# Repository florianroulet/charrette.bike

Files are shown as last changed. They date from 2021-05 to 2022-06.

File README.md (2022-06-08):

# CHARRETTE: CHARRETTE Hardi Auto-freinante Remorquable Réservable Esthétique Tractable Tenace Électrique

origine : https://framagit.org/Veloma/Charrette

## Description
Charrette est une remorque à vélo à trois roues avec système  de  freinage  inertiel et un système d’assistance électrique autonome.
 * Pensée  pour  l’autoconstruction  et  une  diffusion large, la remorque s’attelle sur toutes les tiges de selle de vélo  ou se tire à la main.
 * Le  mécanisme  du  frein  à  inertie  automatique  protège remorque et cycliste en permettant d’augmenter la charge utile jusqu’à 300 kg.
 * Le format de chargement est prévue pour la vélologistique sur palette ou boites transport Euro.
 * Une assistance électrique est conçue pour que la charrette accompagne indépendamment le vélo en modulant sa  propre puissance.
 * D’autres éléments déployables, solaires ou fonctionnels  assurent une grande variété d’usages (restauration, culturel, social....).
 * La remorque en source libre est conçue en tubes carrés simples à provisionner et facilement soudable.

### Historique selon la Charrette
Moi, la charrette, remorque à vélo dont la conception a été commencée et est maintenue à ce jour par Véloma, je suis le fruit d'un long cheminement, d'itérations successives, d'expérimentations pour obtenir un engin roulant tractable à vélo stable et efficace.
Ce chemin a croisé celui d'amis, de personnes désireuses de donner un avis ou dans le besoin de livrer des plantes en moins d'une heure de l'autre côté d'une ville trop chargée par des véhicules vides. Sur la route, j'ai rencontré l'ADEME, au travers d'un Appel à Manifestation d'Intérêt de l'agence francilienne lancé en mai 2020. Cet AMI avait pour thème les basses-technologies, ou low-tech.

Voici quels sont les objectifs énoncés par [cet appel à projet](/pdf/AMI.pdf)

>Ouvert, ascendant et promouvant des approches **résolument systémiques de l'innovation**, le présent AMI poursuit plusieurs objectifs **dans une perspective d’autonomie, d’autosuffisance, d’adaptabilité, de transformabilité et de résilience territoriales** :
>
>* Questionner l’organisation socioéconomique et territoriale des activités humaines à l’aune de l’échelle bien proportionnée pour la mise en œuvre d’une démarche « low- tech » : modèles organisationnels, modèles d’affaires, synergies et solidarités interterritoriales, etc. ;
* Interroger les besoins en ressources au regard des limites physiques (finitude des ressources, etc.), technico-économiques (phénomène de saturation des capacités des systèmes techniques, taux de retour énergétique décroissants des ressources énergétiques, endettements, rendements théoriques maximaux, rendements décroissants des systèmes complexes, etc.) et humaines (résistances au changement de comportement) : sobriété, écologie de la demande, etc. ;
* Étudier, dans toutes leurs dimensions (technologique, fiscale, législative, réglementaire, normative, etc.), les conditions d’émergence ainsi que les freins et les leviers au (re)déploiement de systèmes sociotechniques et économiques plus intensifs en emplois et plus sobres en consommation de ressources. Il s’agira ici de s’interroger sur la quantité et la qualité du travail humain et de caractériser ce que seraient des métiers et des emplois « low-tech » ainsi que les trajectoires de reconversion professionnelle associées dans les prochaines décennies à l’aune de la notion d’« esclave énergétique » et dans un contexte d’accès aux ressources (énergétiques notamment) de plus en plus limité. En particulier, seront-ils plus ou moins salariés, plus ou moins rémunérés, plus ou moins partagés, plus ou moins réflexifs et scientifiquement éclairés, plus ou moins manuels, plus ou moins physiques ?
* Contribuer à remettre de la lucidité et de redonner du sens à l’innovation et à réinventer des métiers et emplois inspirants compatibles avec la réalité physique d’un monde fini par la transformation des récits collectifs aujourd’hui dominés par le paradigme de l’inflation technologique et de l’accumulation matérielle.

Alors que j'étais en prototypage dans l'atelier de Véloma, alors que le monde entier et la France en particulier étaient enfermés entre quatre murs, mes trois pneus se gonflaient, on m'accrochait derrière un vélo et je m'élançais dans les rues séquano-dyonisiennes pour livrer denrées et semis.
Pendant ce temps, Véloma a envoyé un dossier à l'ADEME et est devenue, comme 9 autres structures, lauréate de cet appel à manifestation d'intérêt.

J'ai ainsi été propulsée sous les feux d'une petite communauté de bricoleurs, de créateurs, de rêveurs qui oeuvrent pour créer un autre monde, un monde où l'on pourrait aller faire ses courses avec son vélo, un monde où l'on pourrait m'emprunter ou me louer dans une maison de quartier, un monde où l'on pourrait télécharger mes plans sur internet pour les donner au soudeur du coin et qu'une soeur naisse ailleurs, un monde où l'on pourrait m'augmenter, me transfigurer, m'adapter à des usages non prévus lors de ma conception.

Ce monde décrit à l'instant, c'est celui vers lequel me porte Véloma avec l'aide de l'ADEME, du réseau mis à disposition et des copains dont tu peux faire partie. Je suis sur cette route depuis novembre 2020 et jusqu'à octobre 2022.

## Libre, auto-constructible et réparable
Les concepteurs initiaux de la remorque croient en un monde inspiré du logiciel libre, un monde qui n'a pas peur de partager ses connaissances pour les voir être appropriées par d'autres, améliorées, modifiées ou détournées.
Ainsi l'intégralité des plans de la charrette seront mis à disposition sur ce site sous licence CERN-OHL-W v2. Le code sera partagé sous licence CC-BY-SA.

## La remorque
La remorque est un engin roulant à trois roues qui s'attele sur la tige de selle d'un vélo.
Elle peut aussi être tractée par un humain voire un animal de traie.
La structure et les roues ont été dimensionnées pour supporter 300kg.
La surface utile de chargement est de 1705x650mm, les ridelles font 330mm de haut, la garde au sol est de 360mm.

### Structure
Les tubes de la structure sont soudés ensemble pour assurer rigidité et longue vie au châssis.
Des plans de découpe laser des tubes existent mais la découpe à la main de chaque tube est possible.

Nous travaillons avec de l'acier inox 304 et 316 mais il est possible d'utiliser n'importe quel acier de qualité, un passage à la peinture sera à considérer.

Pour la soudure, nous avons des postes TIG et MIG dans notre atelier mais lors des formations, la soudure à l'arc avec baguette inox est utilisée.

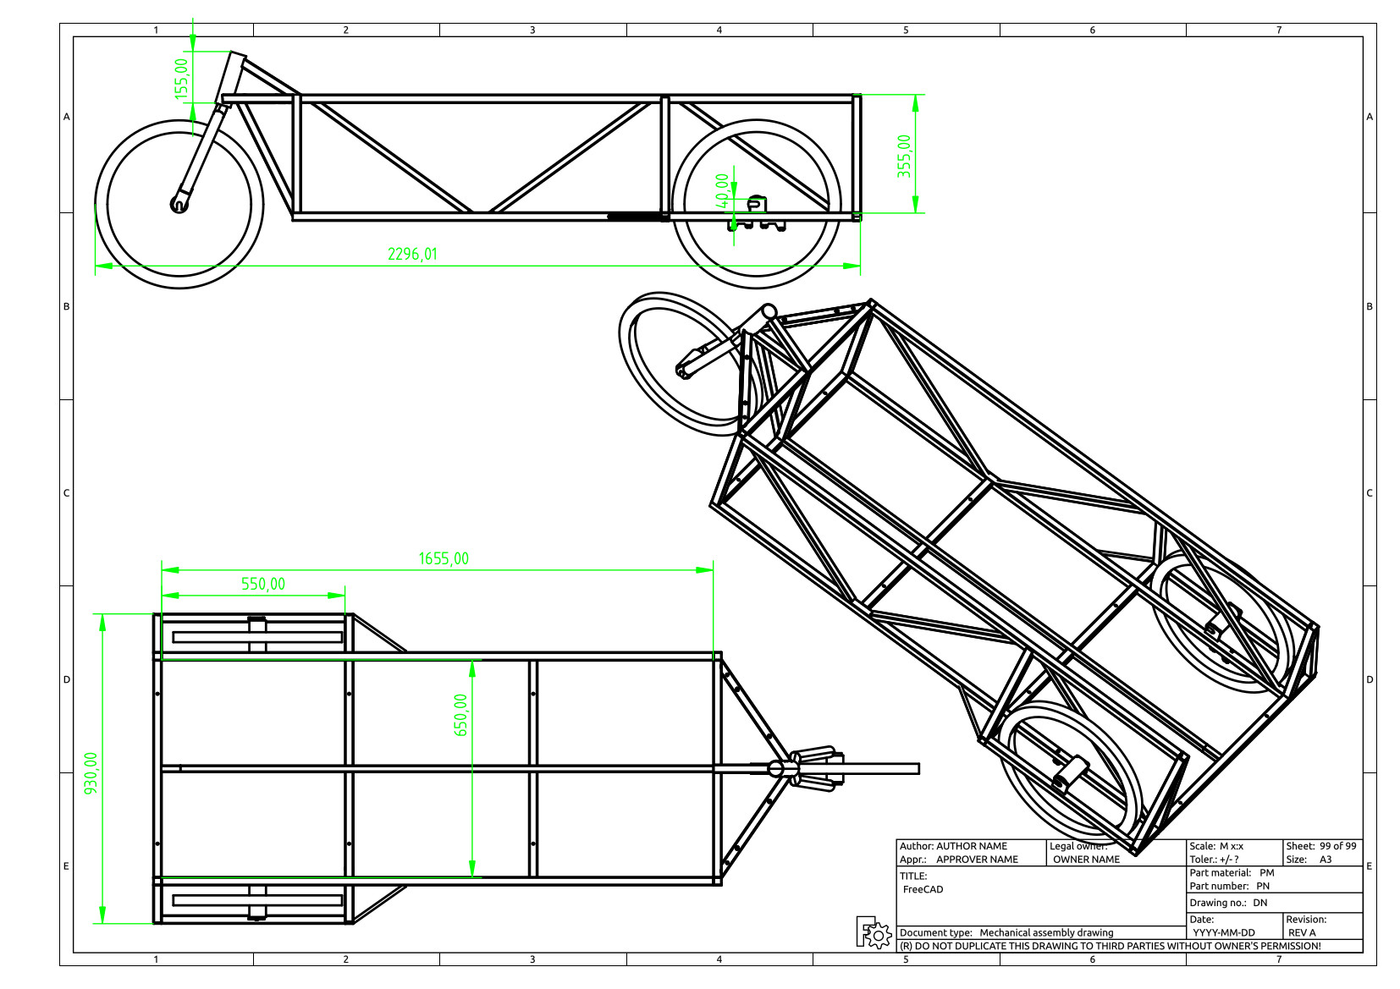
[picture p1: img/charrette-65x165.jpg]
Châssis de la remorque


Une réflexion est menée pour la fabrication de fourche 20":

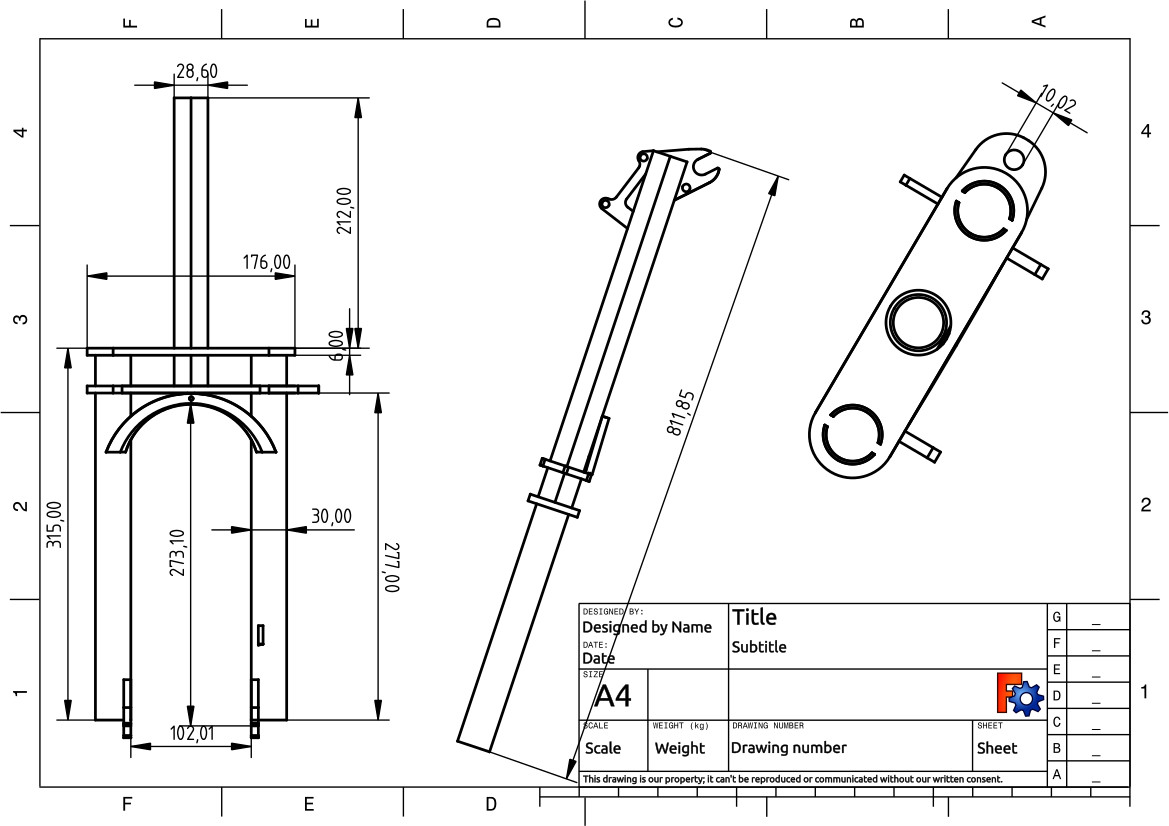
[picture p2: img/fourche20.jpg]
Fourche 20"


### Equipement vélo
La charrette est un équipement de cycles et à ce titre est équipée comme un vélo:
* Jantes kargo;
* Rayons inox renforcés;
* Moyeux renforcés;
* Garde-boue en aluminium;
* Axes de roues diamètre 15 en acier plein et faits chez un tourneur;
* Freinage à câble;
* Etrier de frein à disque BB5;
* Jeu de direction interne;
* Potence courte.

Tous ces équipements sont au maximum sourcés en France ou en Europe.
Une attention toute particulière a été portée aux roues que nous assemblons nous-mêmes afin qu'une charge de 300kg soit supportées dynamiquement entre les trois roues et axes.

### Système de freinage inertiel
Un mouvement relatif entre la barre d'attelage et la remorque est autorisé par un roulement linéaire dans le sens de la marche.
Un ressort limite les mouvements et tend à maintenir la remorque dans une position au repos.
En cas de freinage du pilote, la remorque vient s'appuyer sur la barre d'attelage et tire deux câbles qui freinent les roues arrières.
Il s'agit là d'un frein à inertie qui est primordial pour la tenue de route et la sécurité du chargement.

### Frein de stationnement
A l'arrêt, pour sécuriser la Charrette, il est possible de maintenir le frein à inertie actionné avec un crochet. Le frein à inertie devient alors frein de stationnement.

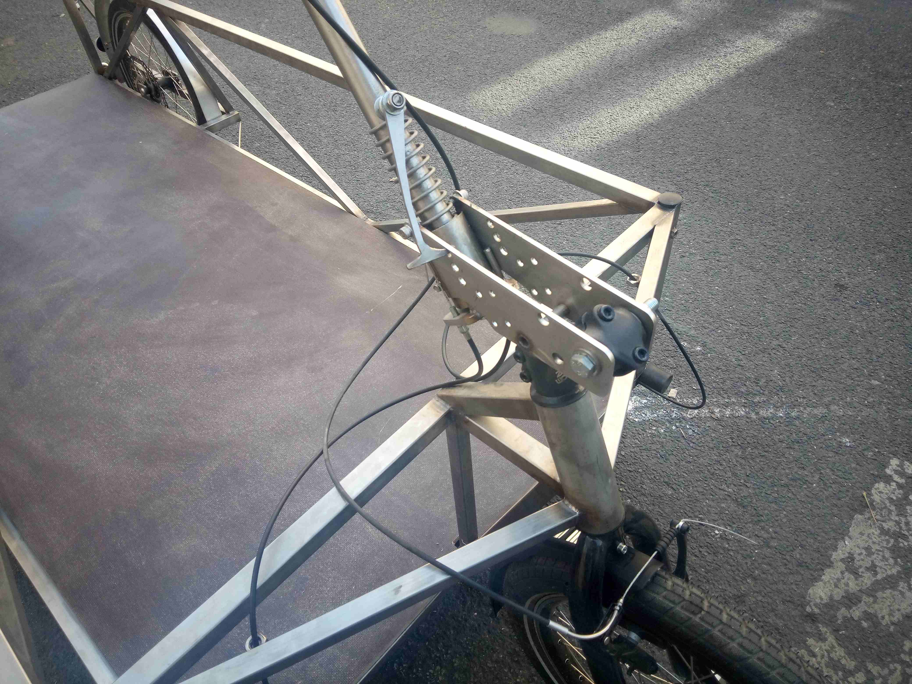
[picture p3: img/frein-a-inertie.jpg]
Frein à inertie et de stationnement


### Tenue de route
Nous n'avons pas encore réussi à retourner la charrette dans un virage.

## Assistance électrique

Là où les vélos sont limités à 250W, les remorques à vélo n'observent pas cette limite tant qu'elles ne sont pas motrices, entendez qu'elles ne poussent pas le vélo.sdfdsf
Le système d'assistance électrique met donc la remorque en équilibre derrière le cycliste et active même le freinage moteur en cas de besoin.
Nous préconisons un moteur de 1200W et une batterie de 48V afin d'avoir assez de puissance pour déplacer jusqu'à 300kg, il faudra tout de même appuyer sur les pédales.

A minima il faudra donc s'équiper:
* d'un moteur moyeu 1000/1500W monté dans une roue 20"
* d'un contrôleur de moteur 48V 25A
* d'une batterie de 48V 20Ah

Deux types d'assistance ont été développés:
 - Une assistance "intelligente" qui détecte le retard de la remorque par rapport au cycliste et assiste en fonction.
 - Une assistance manuelle qui est pilotée par une gachette au guidon du cycliste.

### Assistance "intelligente"

En équipant la barre d'attelage de jauge de contrainte, il est possible de piloter l'assistance électrique avec un arduino.
Ce système est mis sous tension par un simple interrupteur, ensuite sitôt que la remorque détecte qu'elle est en retard par rapport au vélo, elle actionnera son moteur jusqu'à rattraper le cycliste et dans le cas contraire où elle ira plus vite, la remorque ralentira voire activera son frein moteur.
Cette assistance, plus simple à l'utilisation car il n'y a aucune modification à apporter au vélo-tracteur, est aussi plus compliquée à mettre en oeuvre soit-même et dépend de composants électroniques supplémentaires à approviosionner et à assembler.

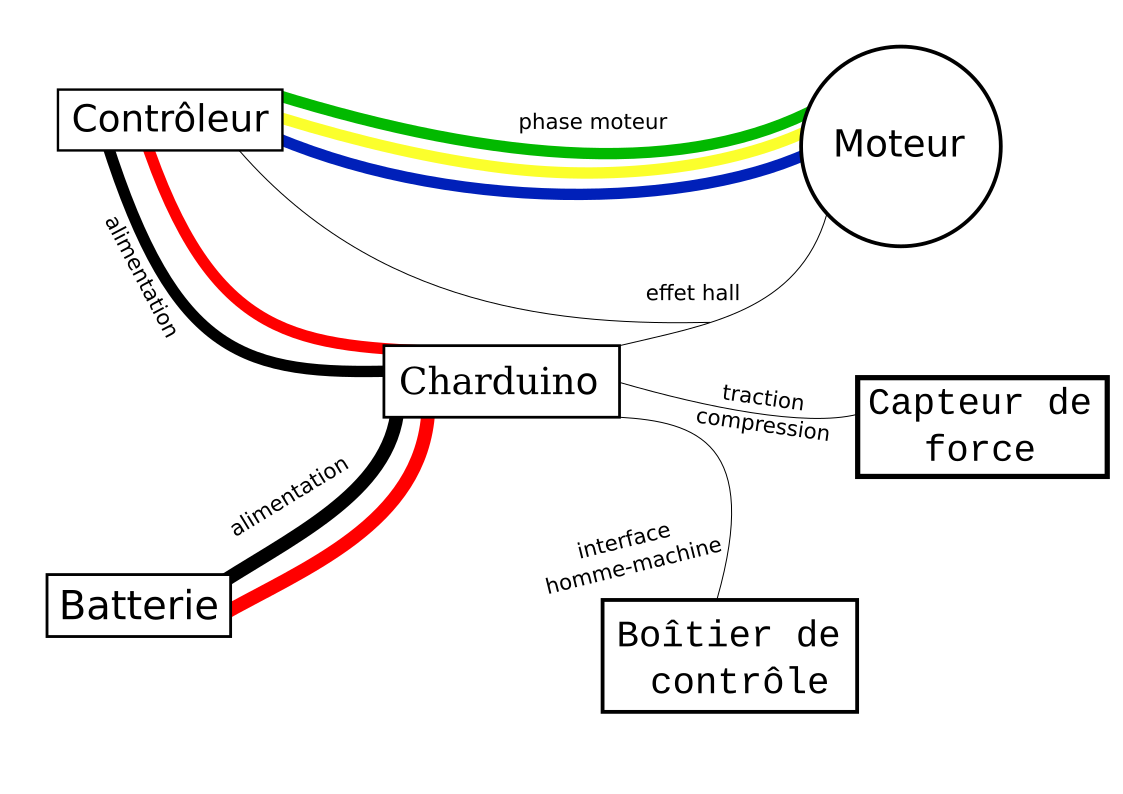
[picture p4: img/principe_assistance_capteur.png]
Schéma de principe


### Assistance manuelle

Les systèmes d'assistance électrique standard peuvent fonctionner avec une gachette d'accélération. L'exemple en est des trottinettes électriques.
Il est possible de piloter la Charrette avec une gachette en tirant un câble jusqu'au guidon.
Pour rester mettre de la remorque, et aussi rester dans le cadre de la loi française, il est impératif que le vélo reste tracteur et ne soit pas propulsé par la Charrette.
En équipant le frein à inertie d'un contacteur, il est possible de couper le signal envoyé au contrôleur. Sitôt que la remorque vient appuyer sur le vélo, le frein à inertie s'enclenche, le contacteur aussi ouvrant le circuit et coupant l'assistance. L'ajout d'un circuit RC entre le contrôleur et le contacteur permet de lisser les accélérations et déccélérations.
Cette solution est plus facile à mettre en oeuvre pour le constructeur mais moins comode pour l'usager qui doit préparer son vélo avant de partir.
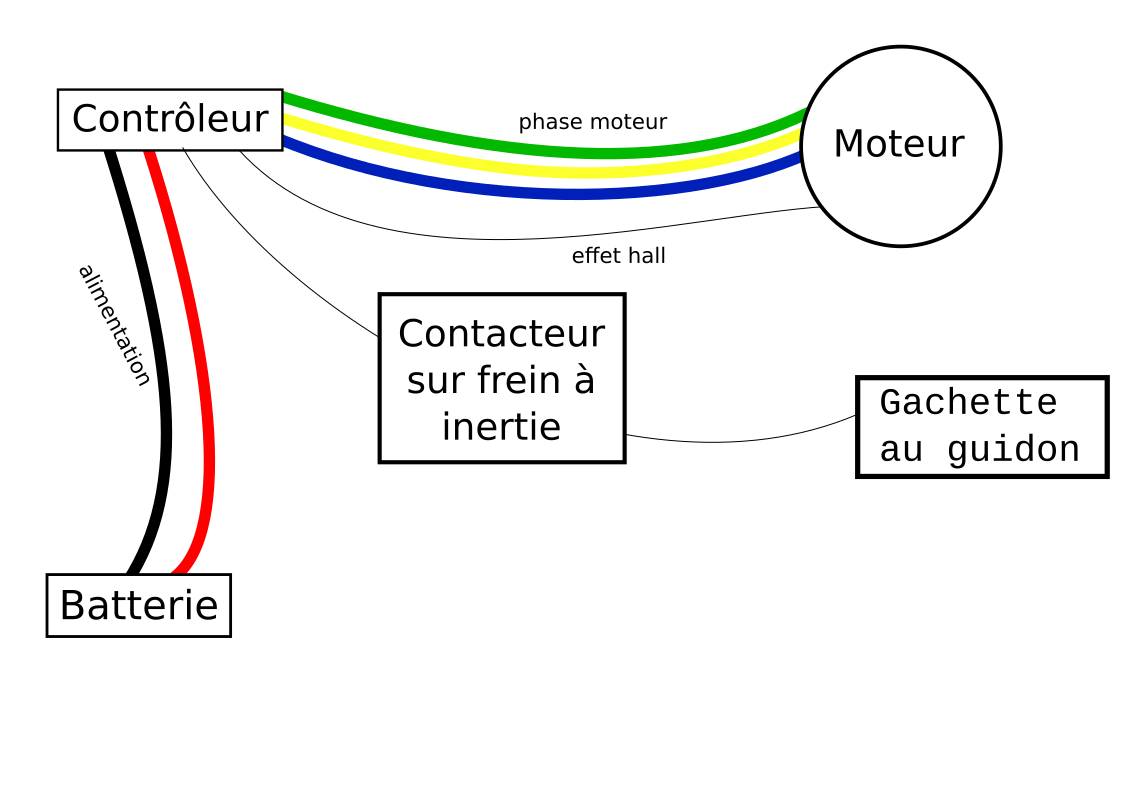
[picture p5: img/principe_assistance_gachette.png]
Schéma de principe


## Système de partage

Un système informatique, pas encore disponible, permettra de mutualiser l'utilisation d'une charrette ou de n'importe quel vélo, pour étendre les imaginaires de toute un quartier. Le code s'appuiera sur celui d'[Open Source Bikeshare](https://github.com/cyklokoalicia/OpenSourceBikeShare).

Ce système de partage a vocation à fonctionner sur un ordinateur type Raspberry Pi et pourra tout aussi bien gérer la mutualisation d'une charrette que de vélos en partage.

## Modulaire

La charrette peut être modifiée facilement et gagner de nouvelles fonctionnalités.

### Charrette-Pikip
Ainsi il est possible d'ajouter des panneaux solaires par exemple et une enceinte [Pikip](https://www.pikip-solarspeakers.com) pour transformer la charrette en remorque Boum-Boum, un engin de célébrations massives.

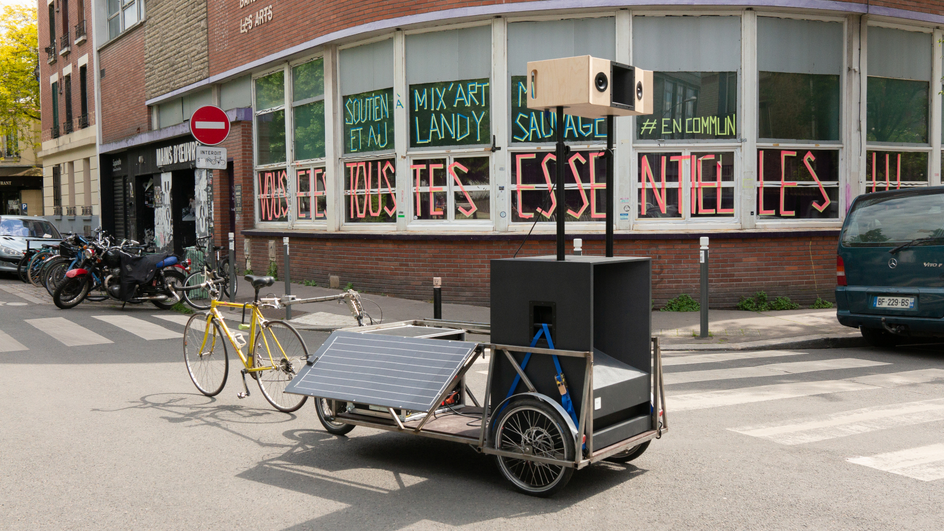
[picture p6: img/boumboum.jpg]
Boumboum


### Panneaux déployables
Les tubes verticaux sont pensés comme chandeliers pour accueillir d'autres tubes et ainsi autoriser le pivotement de panneaux.
Un exemple d'une charrette utilisée par l'association Déenbulles, une ludothèque itinérante.

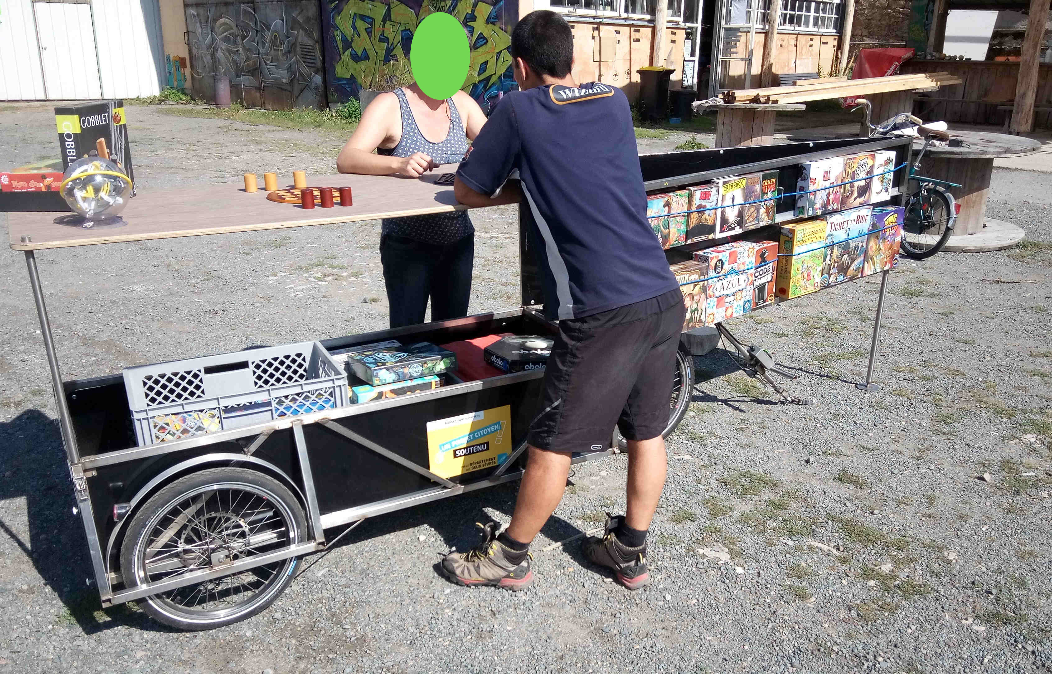
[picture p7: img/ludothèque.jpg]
Ludothèque


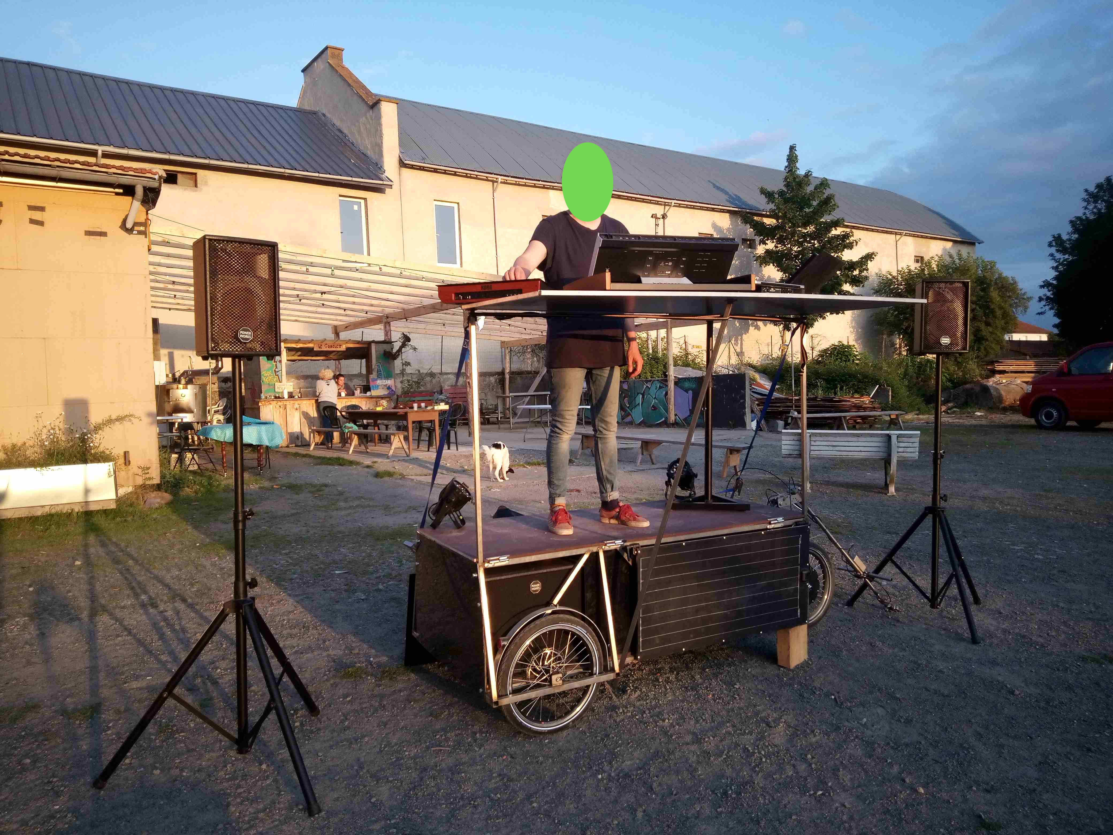
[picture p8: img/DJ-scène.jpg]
DJ Scène


### Examples d'utilisations:

Davantage de photos sur [Charrette.bike](https://charrette.bike)
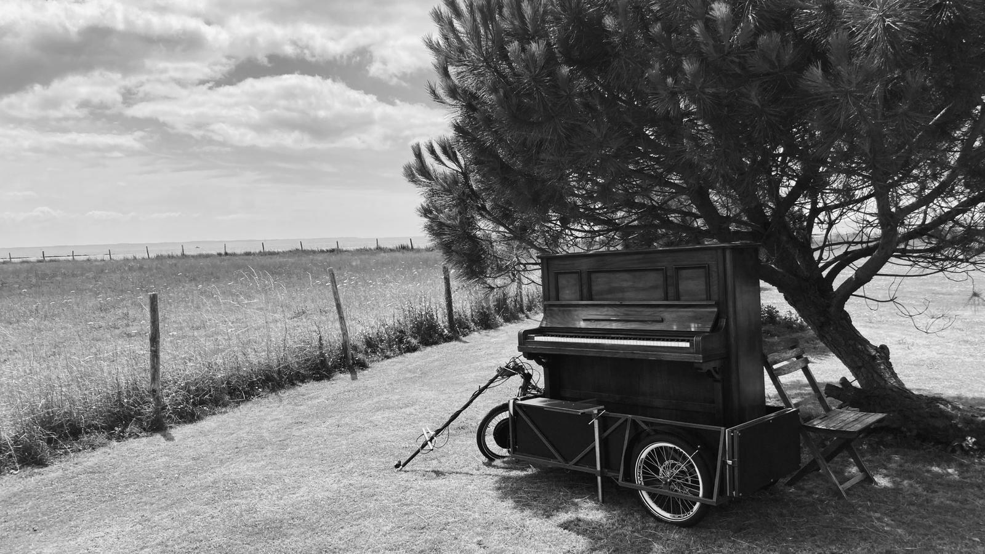
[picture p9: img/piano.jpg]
Piano


## Coût de revient

Le temps passé à chercher et acheter les composants n'est pas pris en compte.

| Partie | Description | Total |
| --- | ---  | --- |
| Structure | Tubes, boulonnnerie, consommable soudure, ...| ???? |
| Equipement vélo | Roues, câbles, gaines, ... | ???? |
| Electronique Charduino| Composants, câbles, connecteurs | ???? |
| Electronique assistance| Moteur, contrôleur, batterie | ???? |
| Total| Matériel | ???? |

## Temps d'assemblage

Le temps passé à chercher, dessiner et/ou acheter les composants n'est pas pris en compte. On considère que les différentes techniques nécessaires sont déjà acquises à la personne qui assemble.

| Partie | Description | Total |
| --- | ---  | --- |
| Structure | Mise en place, sous contrainte, soudure, nettoyage | 2 jour |
| Equipement vélo | Rayonnage des deux roues arrière, installation des composants, réglage des freins | 1,5 jours |
| Electronique Charduino| Soudure des composants, connectiques | 1 jour |
| Electronique assistance| Préparation connectique, branchement | 0,5 jour |
| Total| Temps passé pour une charrette | 5 jours |

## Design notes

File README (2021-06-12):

Arduino pour contrôler la remorque en fonction du capteur de traction

Bibliothèques requises:

#include <EEPROM.h>
#include <Chrono.h>
#include <SoftFilters.h>
#include <PID_v1.h>
#include <Adafruit_NeoPixel.h>
#include <HX711_ADC.h>

2020 11 09
Jusqu'à présent l'arduino était alimenté par le contrôleur via le 5V de la gachette.
Lors des essais il a été constaté qu'il redémarrait quand le moteur tirait trop de jus.
On va passer sur une alimentation directement par la batterie, incorporation d'un step-down pour passer de 36V à 5V et avoir ainsi une alim stabilisé.

Le 5V de la gachette sera tout de même utilisé pour savoir si le contrôleur est allumé ou pas, utilisation d'une résistance pull-down sur une pin.
Possibilité d'utiliser un transistor pour activer le contrôleur quand l'arduino est prêt et que la barre de traction est prête.
Ainsi quand on verra que le contrôleur ne répond pas, on pourra l'éteindre et le rallumer.

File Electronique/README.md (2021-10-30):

# Electronique

Sera évoquée ci-dessous l'électronique de l'assistance électrique utilisant un capteur de force. Il s'agit du Charduino, contraction de Charrette et Arduino.

Pour rappel voici un schéma de principe:

Schéma de principe

## Généralités

Le charduino est le circuit imprimé qui gère l'électronique de la charrette.
Les composants principaux du système sont:
 * Un arduino nano
    * Il traite toutes les données venant des différents capteurs et envoie les ordres au contrôleur
 * Un contrôleur de moteur électrique
    * Il active le moteur ou le frein moteur en fonction du signal de la gachette et du signal de frein
    * Ces deux signaux sont générés par l'arduino, en fonction des capteurs
 * Une batterie 36 ou 48V
    * Plomb ou lithium
    * 48V pour avoir plus de couple
 * Un moteur électrique de vélo
    * 1200W pour assurer de déplacer 300kg
 * Un capteur de force
    * Des jauges de déformation qui quantifient la compression ou la traction de la barre d'attelage.
    * Cette information est envoyée à l'arduino
 * Les capteur effet hall du moteur
    * Capteurs intégrés dans le moteur.
    * Ils renseignent sur la vitesse et le sens de rotation de la roue.
 * Un boîtier de contrôle
    * Pour renseigner l'utilisateur sur l'état du système
    * Pour sélectionner différents mode de fonctionnement (activation, frein, mode piéton)

## Fonctionnement d'un vélo électrique
Un vélo électrique fonctionne grâce à
 * Un vélo
 * Une batterie
 * Un moteur
 * Un contrôleur
 * Des accessoires de commande qui peuvent être:
    * Une gachette d'accélération
    * Un frein
    * Un capteur de pédalage

Le contrôleur agit comme chef d'orchestre, il est relié à la batterie, au moteur et aux accessoires de commande.
En fonction de ces derniers et des signaux envoyés, le contrôleur transforme le courant de la batterie en signaux de puissance triphasé, le moteur tourne alors.

### La gachette

La gachette d'accélération est un potentiomètre, une résistance variable.
Ainsi elle a 3 fils:
 * VCC ou 5V
 * Un signal échelonné entre 0 et 5V
 * GND

Si la gachette n'est pas activé, on envoie 0V au contrôleur, la roue ne tourne pas.
Si la gachette est actionnée au maximum, on envoie 5V au contrôleur, la roue tourne avec toute la puissance possible
Et entre les deux, le contrôleur envoie plus ou moins de puissance dans le moteur.

### Le frein
Le système de frein est basé sur un interrupteur, il y a donc 2 fils:
 * Signal
 * GND

La poignée de frein est équipée d'un interrupteur. Dès que le levier de frein est actionné, le circuit est fermé, le signal est mis à la masse, le contrôleur arrête d'accélérer et active le frein moteur s'il en est capable. Auquel cas la batterie se recharge.

METTRE SCHEMA DE PRINCIPE D'UN CONTROLEUR AVEC LES CONNECTEURS

Pour davantage d'information sur le fonctionnement du vélo électrique, je vous invite à lire [cette page](https://ebikes.ca/getting-started/ebikes-parts-explained.html) en anglais. Le site [ebikes.ca](https://ebikes.ca) est une ressource fiable à recommander.

## Fonctionnement de l'assistance électrique de la charrette

### Considérations légales

Un vélo ne peut être assisté avec plus de 250W sinon il s'agit d'un vélomoteur qui doit être immatriculé et assuré.
Une remorque à vélo peut être motorisée avec davantage de puissance à la condition qu'elle reste un accessoire et qu'elle ne soit pas motrice, c'est à dire qu'elle ne pousse pas le vélo, elle le suit et accompagne le mouvement.

### Solution technique retenue

Pour rentrer dans le cadre légal et rendre la charrette autonome et indépendante du vélo tracteur, la charrette est équipée d'un ***capteur de force*** qui mesure la déformation longitudinale de la barre d'attelage, c'est à dire la compression ou la traction dans le sens de la marche.
Le système repose sur l'idée simple suivante, mettre en équilibre la charrette par rapport au mouvement du vélo en s'appuyant sur le capteur de force et la vitesse de rotation de la roue

### Boîtier de contrôle

Un boîtier de contrôle est fixé sur la barre d'attelage.
Celui-ci permet:
 * d'activer le système
 * de sélectionner un mode d'assistance lent ou normal
 * de forcer l'utilisation du frein moteur
 * de renseigner l'utilisateur sur l'état du système

## Liste composants
### Charduino
| Composant | Description | Quantité | Autre |
| --- | --- | --- | --- |
| Charduino | Circuit imprimé principal de la charrette | 1 |
| Arduino Nano | Microcontroleur | 1
| HX711 | Amplificateur pour capteur de force | 1 | Title |
| Relais Omron G5V-2-H1| Activation du contrôleur de moteur | 1 | |
| Transistor NPN générique | activation du frein moteur | 1 | |
| Résistance 5mOhm | Mesure de courant | 1 | |
| Résistance 1kOhm | Pont diviseur de tension | 1 | R5 |
| Résistance 470 kOhm| Amplificateur opérationnel | 2 | R7 - R10|
| Résistance 10 kOhm | Amplificateur opérationnel et pont diviseur de tension | 3 | R6 - R9 - R4 |
| Résistance 2,2kOhm | Tirage par le bas et filtre RC | 3 | R1 - R2 - R3 |
| LM7525HVT| Transformateur 5V | 1 | |
| Condensateur 100µF 63V | Transformateur 5V | 1 | |
| Condensateur 330µF 25V | Transformateur 5V | 1 | |
| Diode 1N5819 | Transformateur 5V | 1 | |
| Bobine 330µH 2A | Transformateur 5V | 1 | |
| MPC602 | Amplificateur opérationnel | 1 | |
| Condensateur 22µF 25V | Filtre RC| 1 | A vérifier |

### Boîtier de contrôle

| Composant | Description | Quantité | Autre |
| --- | --- | --- | --- |
| Carte | Circuit imprimé du boîtier de contrôle | 1 | |
| Diode | Affichage utilisateur | 1 | |
| Interrupteur | Interface homme/machine | 3 | |
| Boîte aluminium | Protection | 1 | |
| Presse-étoupe| étanchéïté du câble| 1 | |

### Connectiques

Pour les connectiques internes  de signaux, la gamme JST-SM apporte satisfaction. Ces connecteurs sont déjà utilisés dans le monde des vélos électriques.
Pour les connectiques internes et externes de puissance (phase moteur, batterie), la gamme Anderson est satisfaisante.
Cf [ce document](https://www.ebikes.ca/documents/GrinConnectorGuide.pdf) en anglais de ebikes.ca pour plus d'information
Cette [page](https://ebikes.ca/learn/connectors.html) venant toujours du Canada est intéressante aussi

Pour les connectiques panneaux de signaux, nous utilisons actuellement les connecteurs [Neutrik NC-MX6](https://www.thomann.de/fr/neutrik_nc6mx.htm) utilisés dans le monde du spectacle.

Pour les connectiques panneaux de puissance, nous utilisons les connecteurs [Varytech PM](https://www.thomann.de/fr/varytec_real_pm.htm) aussi utilisés dans l'univers de la régie technique.

En fonction du montage, un nombre plus ou moins grand de ces connecteurs est utilisé.

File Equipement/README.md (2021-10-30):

# Equipement vélo
| Composant | Description | Quantité | Autre |
| --- | --- | --- | --- |
| Moyeu |	roulement industriel axe 15mm entraxe 100mm | 2 ou 3 |  |
| Jante |	Mach 1 Kargo 36 trous double paroi | 3 |  |
| Rayons |	Rayons 13G renforcé Mach 1 |  108 |  |
| Pneus | Schwalbe marathon anti crevaison | 3 |  |
| Disque de frein | Disque 203mm inox | 2 |  |
| Gaine de frein | 	gaine de freins Shimano |  3m |  |
| Câble de frein | 	cable inox tandem 3m | 2 |  |
| Frein avant | V-brake | 1 |  |
| Frein à main | Poignée de frein à verrouillage | 1 |  |
| Jeu de direction | 	Jeu de direction roulement intégré 44mm | 1 |  |
| Garde-boue | 	aluminium 50x3mm | 2 |  |
| Etrier de frein | 	Avid BB5 | 2 |  |
| Feu arrière | 	Feu arrière solaire autonome | 2 |  |
| Potence | Potence ahead zoom 1’1/8 | 1 |  |
| Fond de jante | Haute pression | 3 |  |
| Roulement potence |  Roulement industriel 10x26mm | 2 |  |
| Fourche | Fourche BMX 20" 28,6mm renforcée avec V-brake | 1 |  |

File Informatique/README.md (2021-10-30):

Charduino

Soit la méthode avec capteur

Soit la méthode avec contacteur

Allons pour la méthode avec contacteur
Mettre un filtre passe-bas c'est bien à l'ouverture du contacteur situé avant la résistance mais pas pour la fermeture.
Faire un filtre-bande c'est mieux.
On va déjà faire un filtre passe-bas

https://www.translatorscafe.com/unit-converter/fr-FR/calculator/rc-circuit/

Pour la gachette:
 R=100 Ohm
 C=330µF
 T=RC=33ms

Pour le frein
On positionne un filtre RC passe-bas devant le transistor qui va servir d'interrupteur pour relier les deux fils du frein (SIG et GND)
Le transistor est passant pour une tension Vbe>0,7V
Il faut calculer le couple RC pour avoir un temps de 1 seconde pour que le condensateur atteigne 0,7V.
Dans l'autre sens quel temps aura-t-on à la décharge pour pour descendre en dessous de 0,7V et couper le frein?

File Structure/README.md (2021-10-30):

# Structure

## Liste du matériel nécessaire:

| Composant | Description | Quantité | Autre |
| --- | --- | --- | --- |
| Plan de travail | Table de soudure | 1 |  |
| Poste à souder |	TIG ou arc | 1 |  |
| Electrode | soudure inox | 1 paquet |  |
| Serre-joint |	saillie de ??mm | 8 minimum |  |
| Pince-étau | type Facom 501 | 2 |  |
|  |  |  |  |
|  |  |  |  |
|  |  |  |  |

## Liste des composants:
| Composant | Description | Quantité | Autre |
| --- | --- | --- | --- |
| Métal châssis |	Châssis inox 304 et 316 | N/A |  |
| Patte arrière |	Epaisseur de 6mm | 2 |  |
| Barre attelage |	Inox 304 25x1,5mm | 1m |  |
| Attache tube de selle |	Universelle de 25,4 a 31,6mm sans outil | 1 |  |
| Tube roulement linéaire |	Diamètre intérieur 40mm | 10cm |  |
| Roulement linéaire | Roulement linéaire 25mm | 1 |  |
| Ressort | Ressort inox diamètre interne 27mm | 10cm |  |
| Frein de stationnement | crochet inox pour frein de stationnement | 1 |  |
| Attelage | Rotule attelage 12mm | 1 |  |
| Fond de caisse |	Contreplaqué bouleau antidérapant 12mm | 650x1650mm |  |
| Axe roue |	Axe 15mm inox 304 tourné et 2 filetage M8x1,25 | 2 |  |

## Etapes à suivre

Cadre emboit : "charetter mise en place cadre premiere soudure"
> verif cote
> verif equerre, plan
charette pointage "charette pointage des tubes sur ctoutes les sections"

verficationdes perpendicualarité et hauteurs
> poser à l'équerre les montants
>bloage au serrejoint ou pince étau

MOntage de tous les portants sous contraintes

Pointage des contreventement sous contrainte

Pointage des pattes de roue avec le moyeu en place pour garder les dimensions (mettre une rondelle de 16 de 1 côté pour garder de la marge) essayer d'etre à 102mm d'entraxe

POintage support direction avant
> contraindre pour être sûr de l'alignement

Contrainte à l'alignement des tubes de soutien de la direction par rapport au chassis "charette preparation pointage table de direction"
> verification de la planeîté des portant
> verfifier équerrage
> !!! Aucune marge de manoeuvre !!!

Pose du tube de direction (48 par 2)
> au moins 5 mm de chaque côté pour pas que les soudures deforment trop le tube

Fin du pointage, mise en contrainte du chassis, début soudure cadre
> souder des 2 côtés

REtourner le cadre mise en contrainte fin des soudures "charette mise en contrainte du cadre à l'envers"

découpe meleuse tube d'accomodement roulement linéaire

piece de direction
> ecrou M10 et ecrou M8 (M10 pour souder le M8)
> Utiliser vis M8 pour centre ecrou M10 sur le tube et pointer les 2 ecours de chaque côté
> devisser les 2 boulons et finir de souder les 4 ecrous
>Tarauder les ecrou M8

bras de traction manuel
> idem piece de direction

soudure de la direction
> souder tout d'un seul tenant et de manière opposé pour limiter la retracation

souder le cul

préparationd ela barre pieton
> noter le milieu et couper avec angle de 45°

Soudure barre pieton avec bras de traction
> verifier l'equerrage

FREIN A INERTIE BASCULANT
Soudage des ecrous
Souage des parois avec le tube
> a fleur de la la table
> entraxe 4,3cm
>

Montage axe de rotation verticaltimon
>Ecrou rondelle|paroit|rondelle roulement rondelle ecroufilete ecroufilete roulement rondelle |paroit|rondelle boulon

technique d emontage axe de rotation vertical
> 2 clés de 17

verification des taraudage apres soudure
> huilage obligatoire

rattrapage des patés au TIG

placement important

boite experimental taquet

soudage filetage M8 long pour parechoc avant

redressage du chassis si erreur
> verification de toutes les dimensions

Rayonnage mgagnon.net roue montage

Cerclage des garde boue
> meplat alu 40*3mm idéal 50*2

Montage des disques

Souder ecrou pour accueillir garde boue M6
> préperçage garde boue

montage du jeu de direction
> tapper bague alu avec roulement circulaire

Frapper quart de cercle fourche avec tube diametre 35/2 -> montage cone de direction classique

MOntage de l'étoile

Compression du jeu de direction

Montage du bras de force

Il est possible de souder des ecrous pour utiliser des putaing de chambre à air et pas des tendeur Kurva

SOudage de la barre de traction
> M12 pour 22 ecterieur=diametre intérieur timon

Graissage au lithium

Perçage du timon pour frein parking (ressort) 8,6mm

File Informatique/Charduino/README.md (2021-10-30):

# Informatique Charduino

Cette partie documente le code embarqué dans l'arduino qui pilote l'assistance électrique.

## Généralités

Le code est organisé selon une machine à état. Le passage d'un état à l'autre dépend:
 * l'interrupteur de mise en marche
 * l'interrupteur de freinage
 * la vitesse et le sens de rotation de la roue
 * l'effort longitudinal appliqué au timon
 * le courant qui sort de la batterie

 L'idée principale pour régir l'assistance électrique est d'utiliser un PID pour asservir le signal gachette envoyé au contrôleur à l'effort longitudinal lu dans le timon avec les jauges de déformation.
 La lecture de la vitesse et du sens de rotation de la roue sont nécessaires pour les changements d'état.
 Le boîtier de contrôle influe directement via des interrupteurs sur les changements d'état et les paramètres du PID pour le rendre plus ou moins doux.

## PID
## Wattmètre
### Tension
Un pont diviseur de tension est utilisé pour mesurer la tension aux bornes de la batterie. Cette information est utile pour limiter l'usage de l'assistance à une plage de tension et ainsi préserver la batterie de décharge profonde. Cette sécurité est censée être intégrée dans les contrôleurs de moteur, il s'agit là d'une redondance de sécurité.
### Courant
Une résistance de shunt est utilisée avec un amplificateur opérationnel pour mesurer le courant sortant de la batterie.
Cette information est utile dans le cas où le contrôleur se met en défaut malgré l'envoi d'une commande par le signal de la gachette.
Ce cas peut se produire en montée et avec un chargement lourd. Le contrôleur n'arrive pas à faire tourner la roue, il envoie plus de courant mais rien n'y fait. Le contrôleur se met en défaut.
Pour détecter ce cas, qui se produit davantage en utilisant un moteur sans capteur à effet hall, il est nécessaire de lire le courant de sortie de la batterie.
### Puissance
On en déduit plus ou moins finement la puissance consommée par le système.
## Lecture vitesse et rotation de la roue
On utilise les capteurs à effet hall embarqués dans le moteur pour savoir comment tourne la roue.

Initialisation / setup:
  * Ouverture port série
  * Cartouche de bienvenue
  * Iniitialisation des entrées/sorties
  * Initialisation des interruptions
  * Initialisation du PID
  * Initialision du wattmètre
  * Initialisation des différents chronomètres

Boucle principale:
  * Mise à jour de la vitesse
  * Lecture de la valeur du capteur de force
  * Lecture de la tension et du courant de sortie de batterie
  * Gestion des "software debounce" pour les interrupteurs du boîtier de contrôle
  * Gestion de la machine à état
  * Impression des messages de debug
  * Vérification de l'état du contrôleur
  * Envoi de l'ordre de la gachette
7 états

Etat 0: Initialisation
Etat 1: Attente avant départ
Etat 2: Roulage
Etat 3: En suspens
Etat 4: Déccélération
Etat 5: Freinage
Etat 6: ?
Etat 7: Réinitialisation du capteur

0 -> 1
  Conditions:
    Etat == Initialisation
    Initialisation du capteur réussie
    Vitesse moyenne < 1km/h
    Contrôleur allumé
  Actions:

1 -> 2
  Conditions:
    Etat

* -> 7
  Conditions:
    Etat == *
    3 commutations succcessives de l'interrupteur "Frein"
    Contrôleur éteint

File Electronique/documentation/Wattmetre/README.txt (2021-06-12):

***************************************************************
* Arduino Wattmeter - Version 0.1
* by Michel <shenron@terbolidore.net>
*
* This Library is licensed under the MIT License
***************************************************************

 - Nothing for now

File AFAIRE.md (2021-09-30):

# Liste des tâches en cours et à faire

* Décider d'un logiciel pour la documentation qui autorise l'exportation
  --> GitBook?
  Il nous faudrait une table des matières

Structure du répertoire git

Racine/
  /Structure/
    Plan de la remorque 2D.pdf
    Plan 3D.freecad
    Plan découpe laser.pdf ?
    Instruction
  /Equipement/
    Liste pièces détachées, prix et quantité
    Instructions montage
  /Informatique/
    Code arduino avec toutes les librairies et les commentaires qui vont bien
  /Electronique/
    Code KiCAD
    Plan gerber de la carte.pdf
    Liste pièces détachées, prix et quantité
    Instructions assemblage
  README
    un descriptif du projet, le fonctionnement général de l'engin, son historique, son état actuel, son futur imaginé...
    le prix d'un kit, d'une charrette montée, avec ou sans assistance...

SCHEMA
  * contrôleur de moteur avec les connecteurs

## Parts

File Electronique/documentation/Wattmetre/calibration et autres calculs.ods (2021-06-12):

0,97 | 64,9484536082 |  |  | 39,58 | 18,3931278423
63 |  |  |  | 728
 |  |  | 15,7538461538
U2=U*R2/(R1+R2)
 | R1 | 1000
 | R2 | 10000
 | U | 39,8
 | U2 | 36,1818181818
 | U1 | 3,6181818182

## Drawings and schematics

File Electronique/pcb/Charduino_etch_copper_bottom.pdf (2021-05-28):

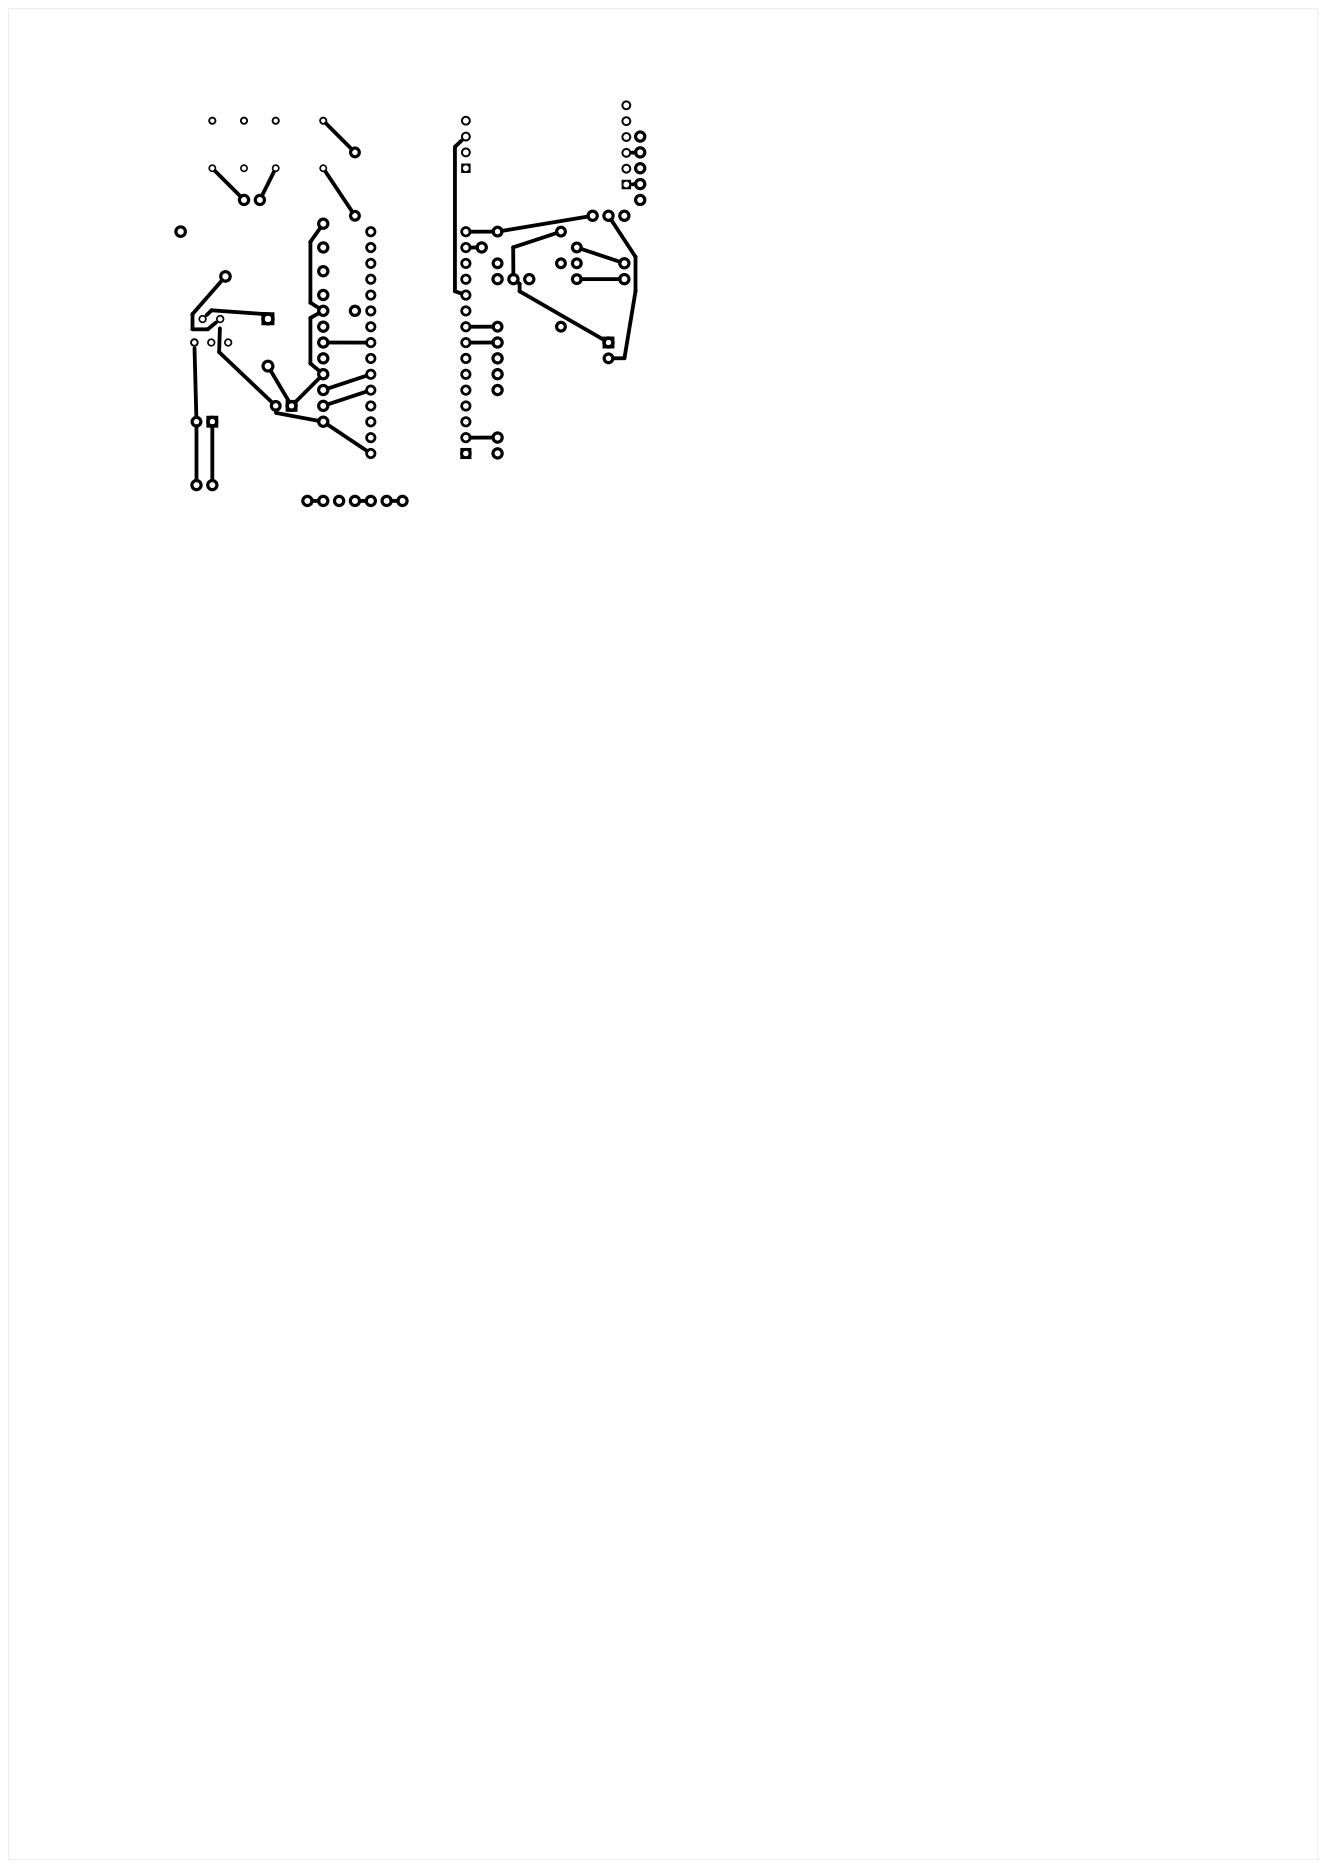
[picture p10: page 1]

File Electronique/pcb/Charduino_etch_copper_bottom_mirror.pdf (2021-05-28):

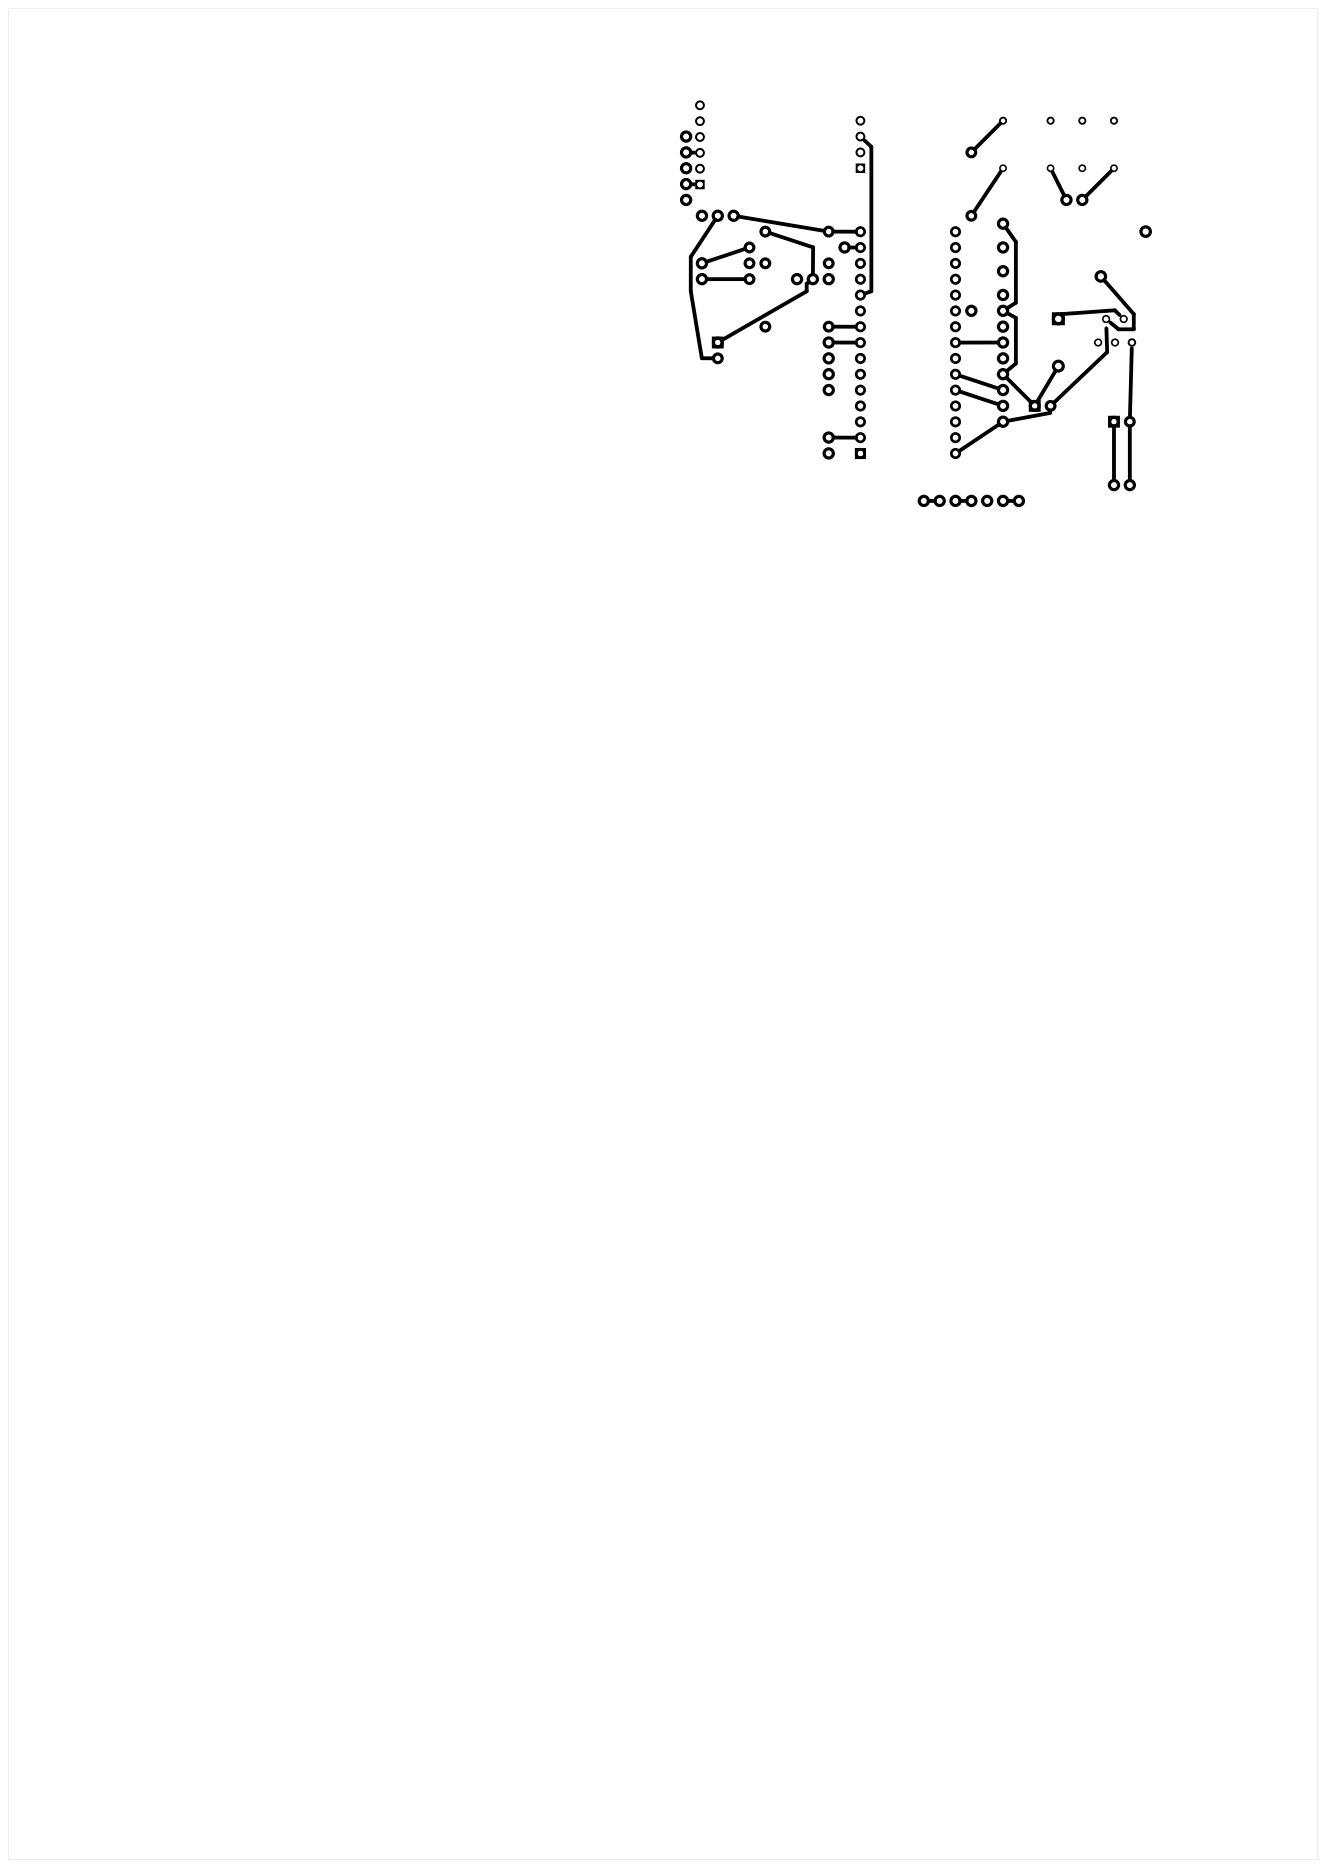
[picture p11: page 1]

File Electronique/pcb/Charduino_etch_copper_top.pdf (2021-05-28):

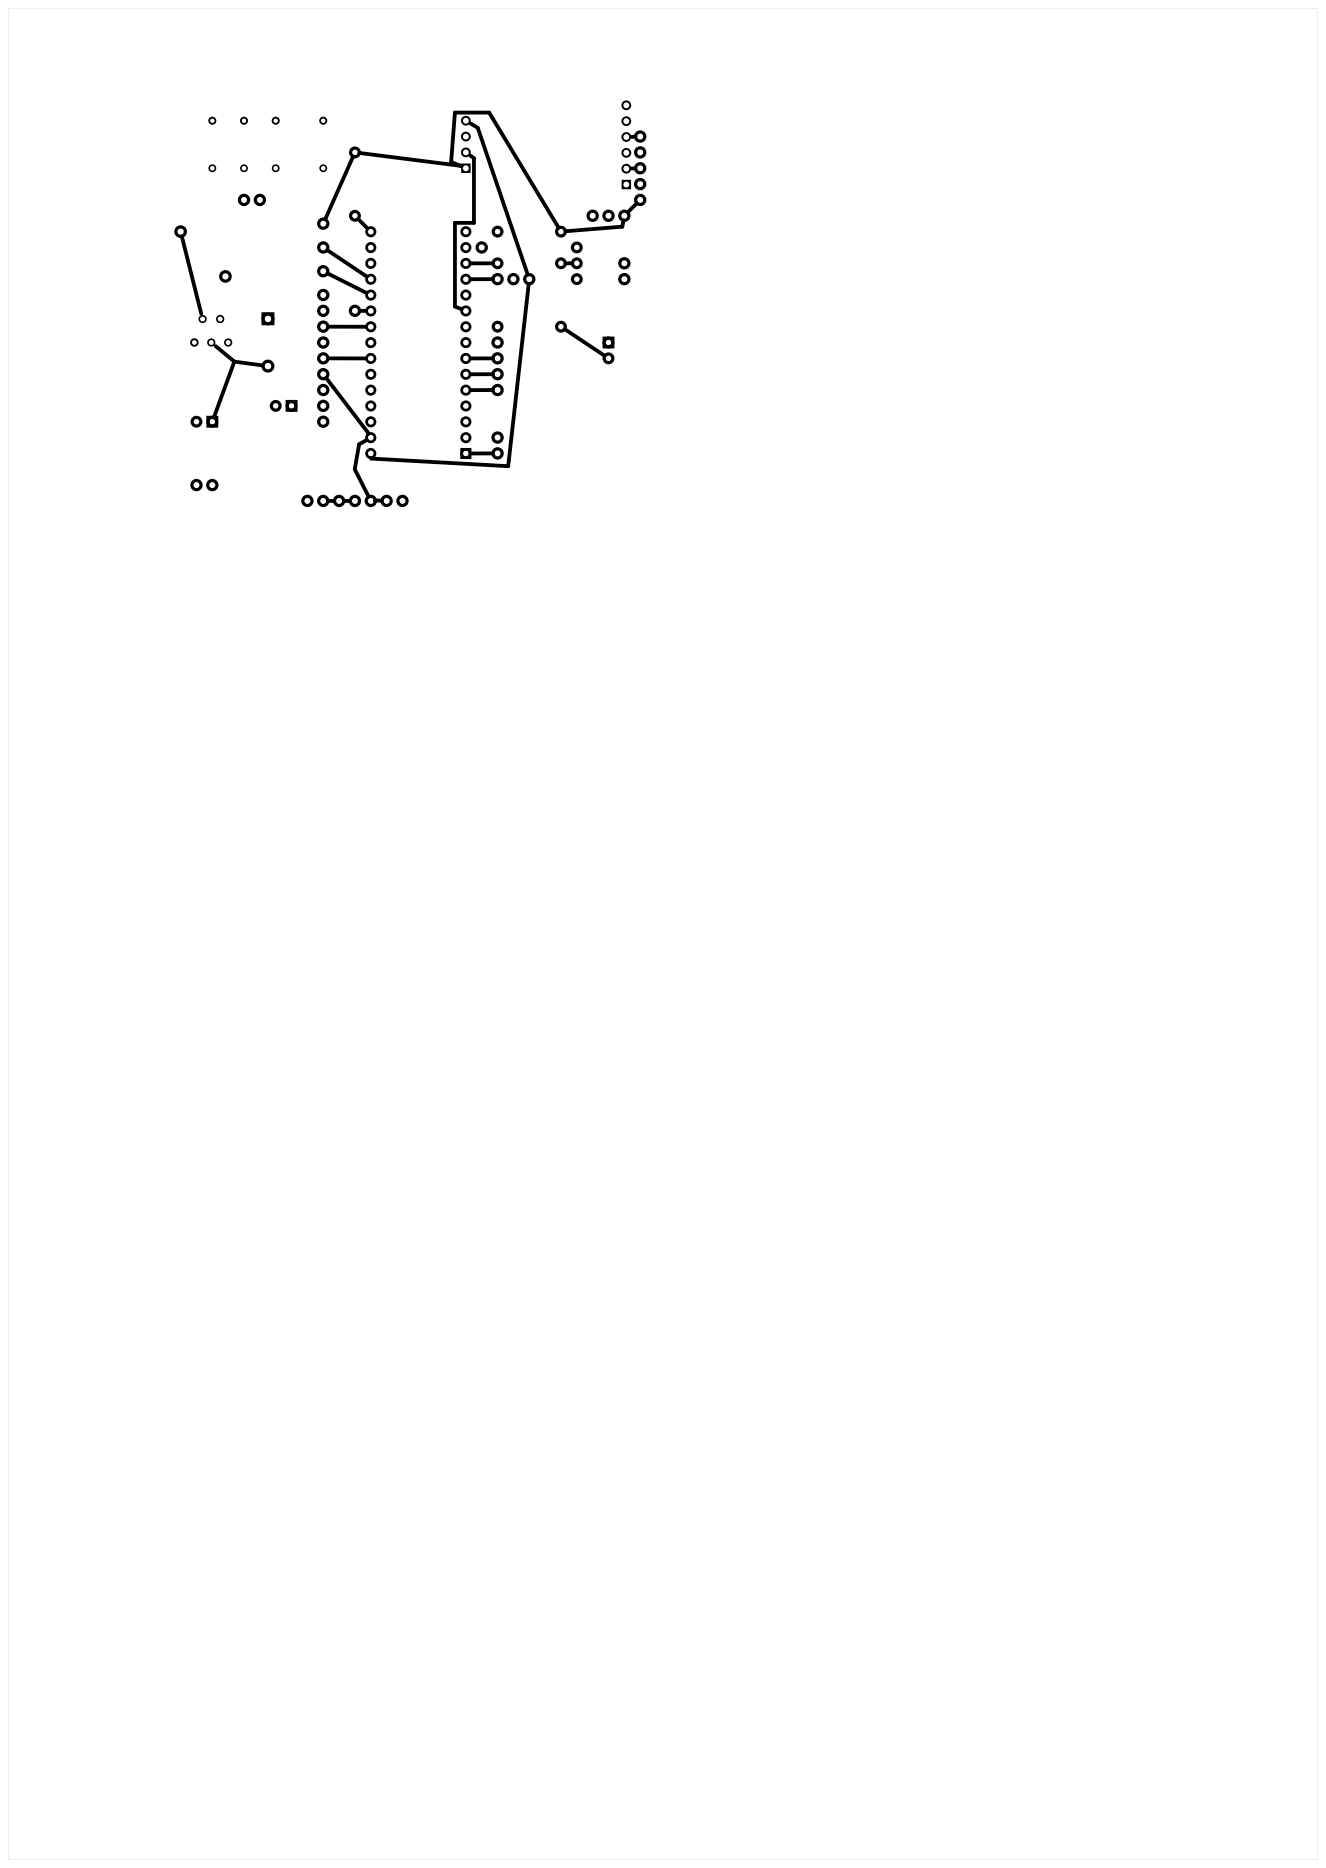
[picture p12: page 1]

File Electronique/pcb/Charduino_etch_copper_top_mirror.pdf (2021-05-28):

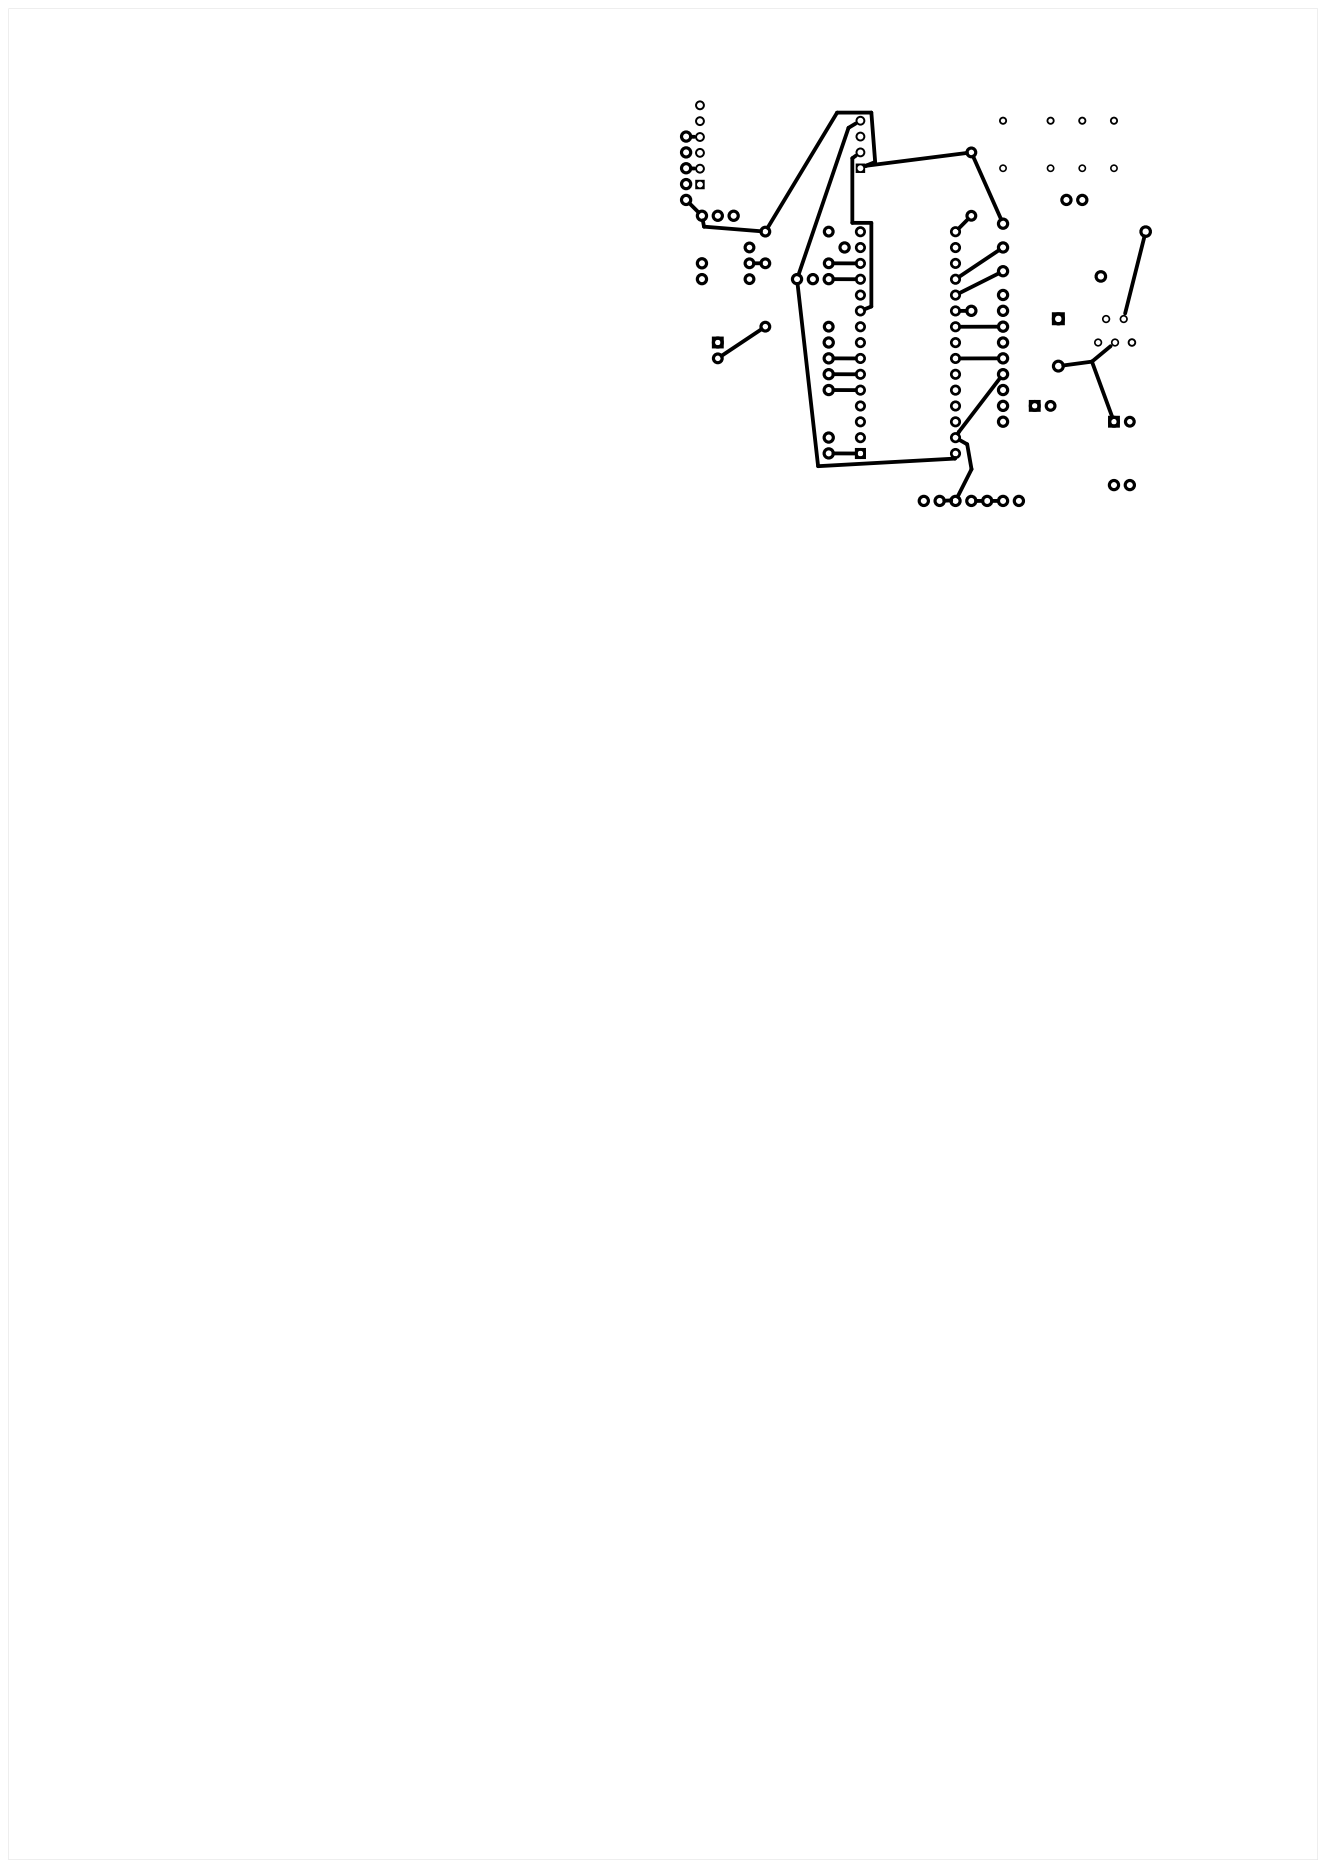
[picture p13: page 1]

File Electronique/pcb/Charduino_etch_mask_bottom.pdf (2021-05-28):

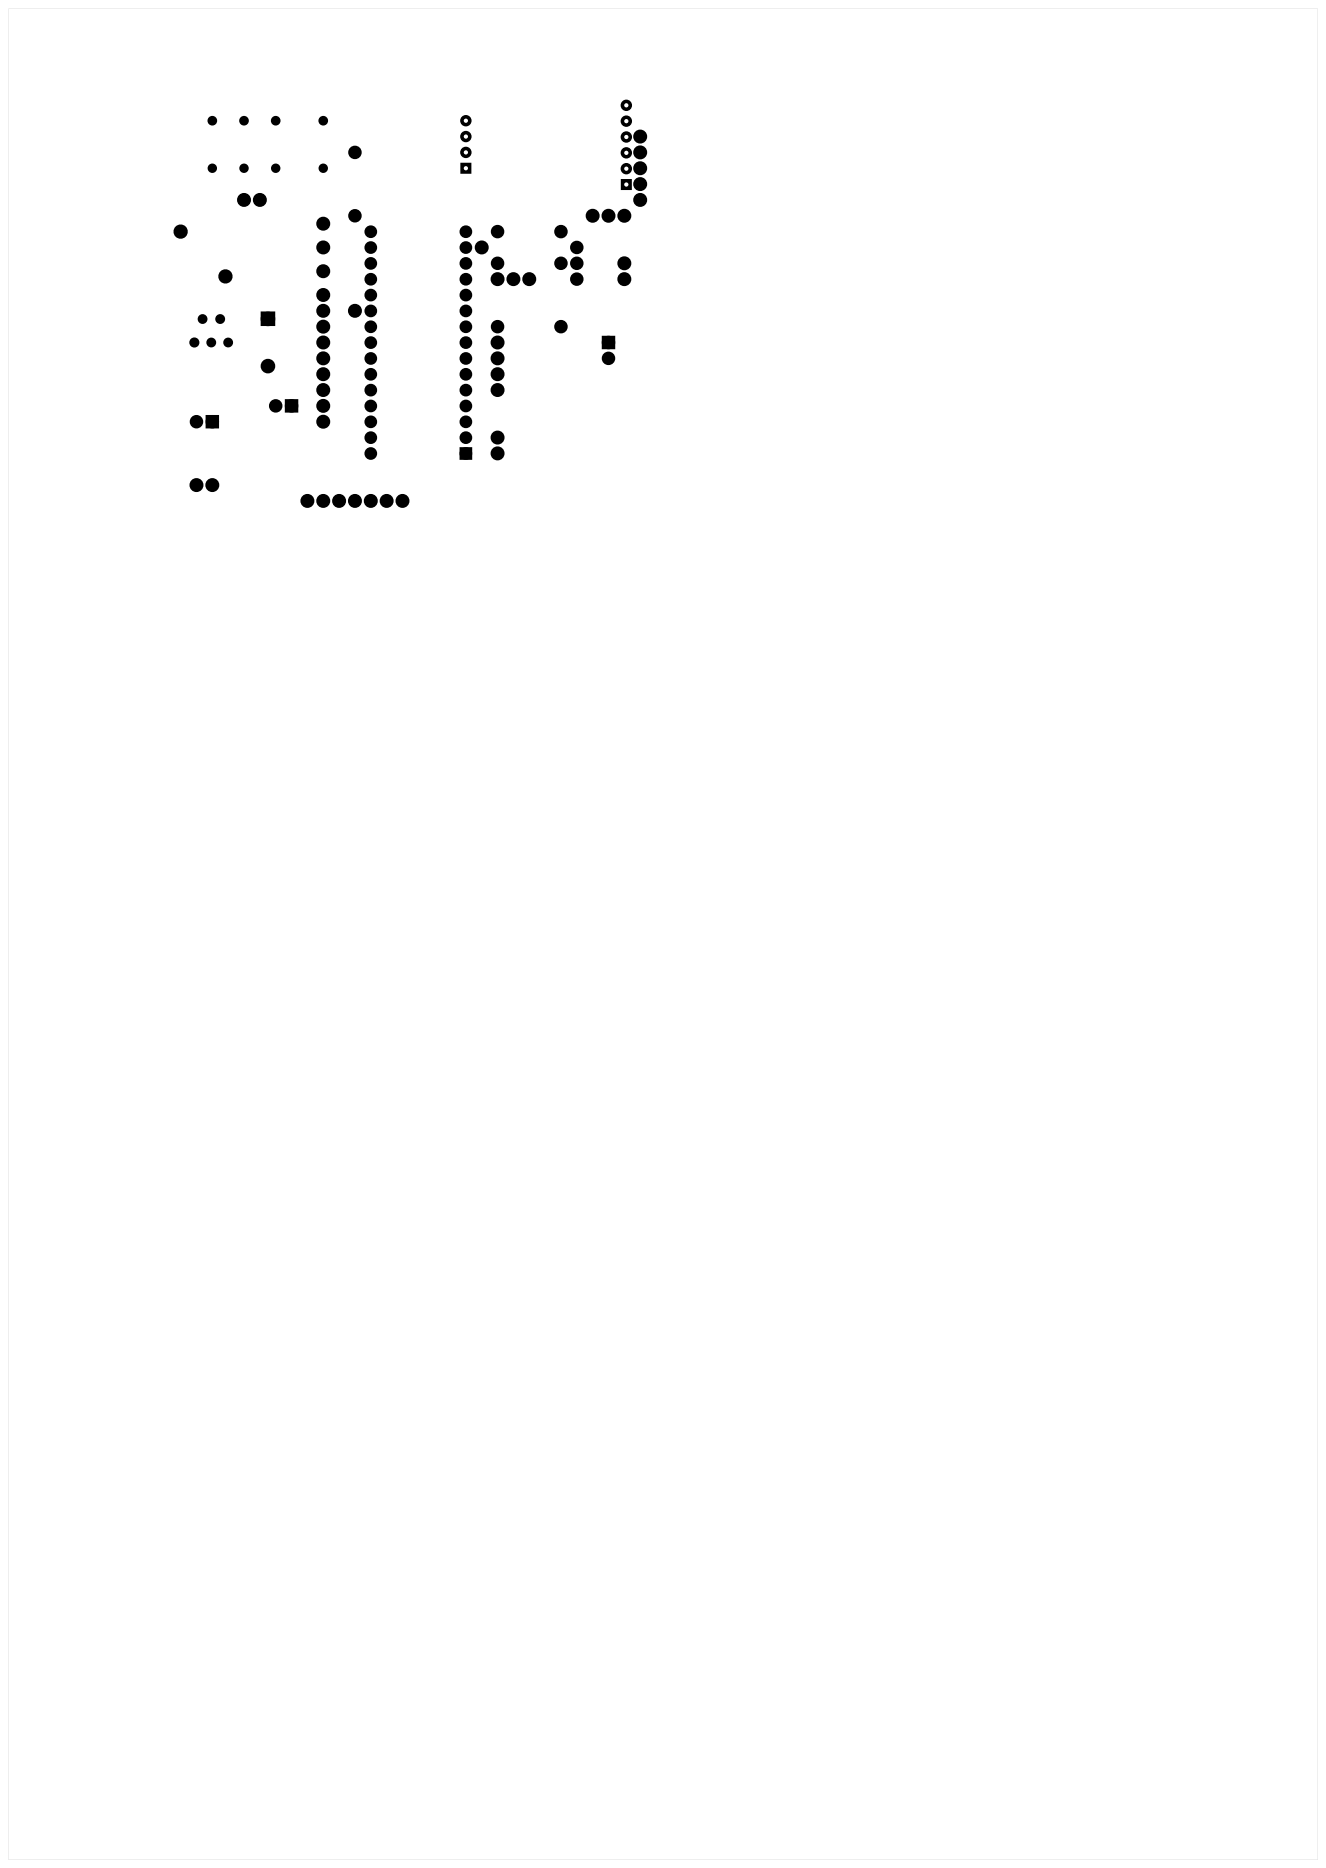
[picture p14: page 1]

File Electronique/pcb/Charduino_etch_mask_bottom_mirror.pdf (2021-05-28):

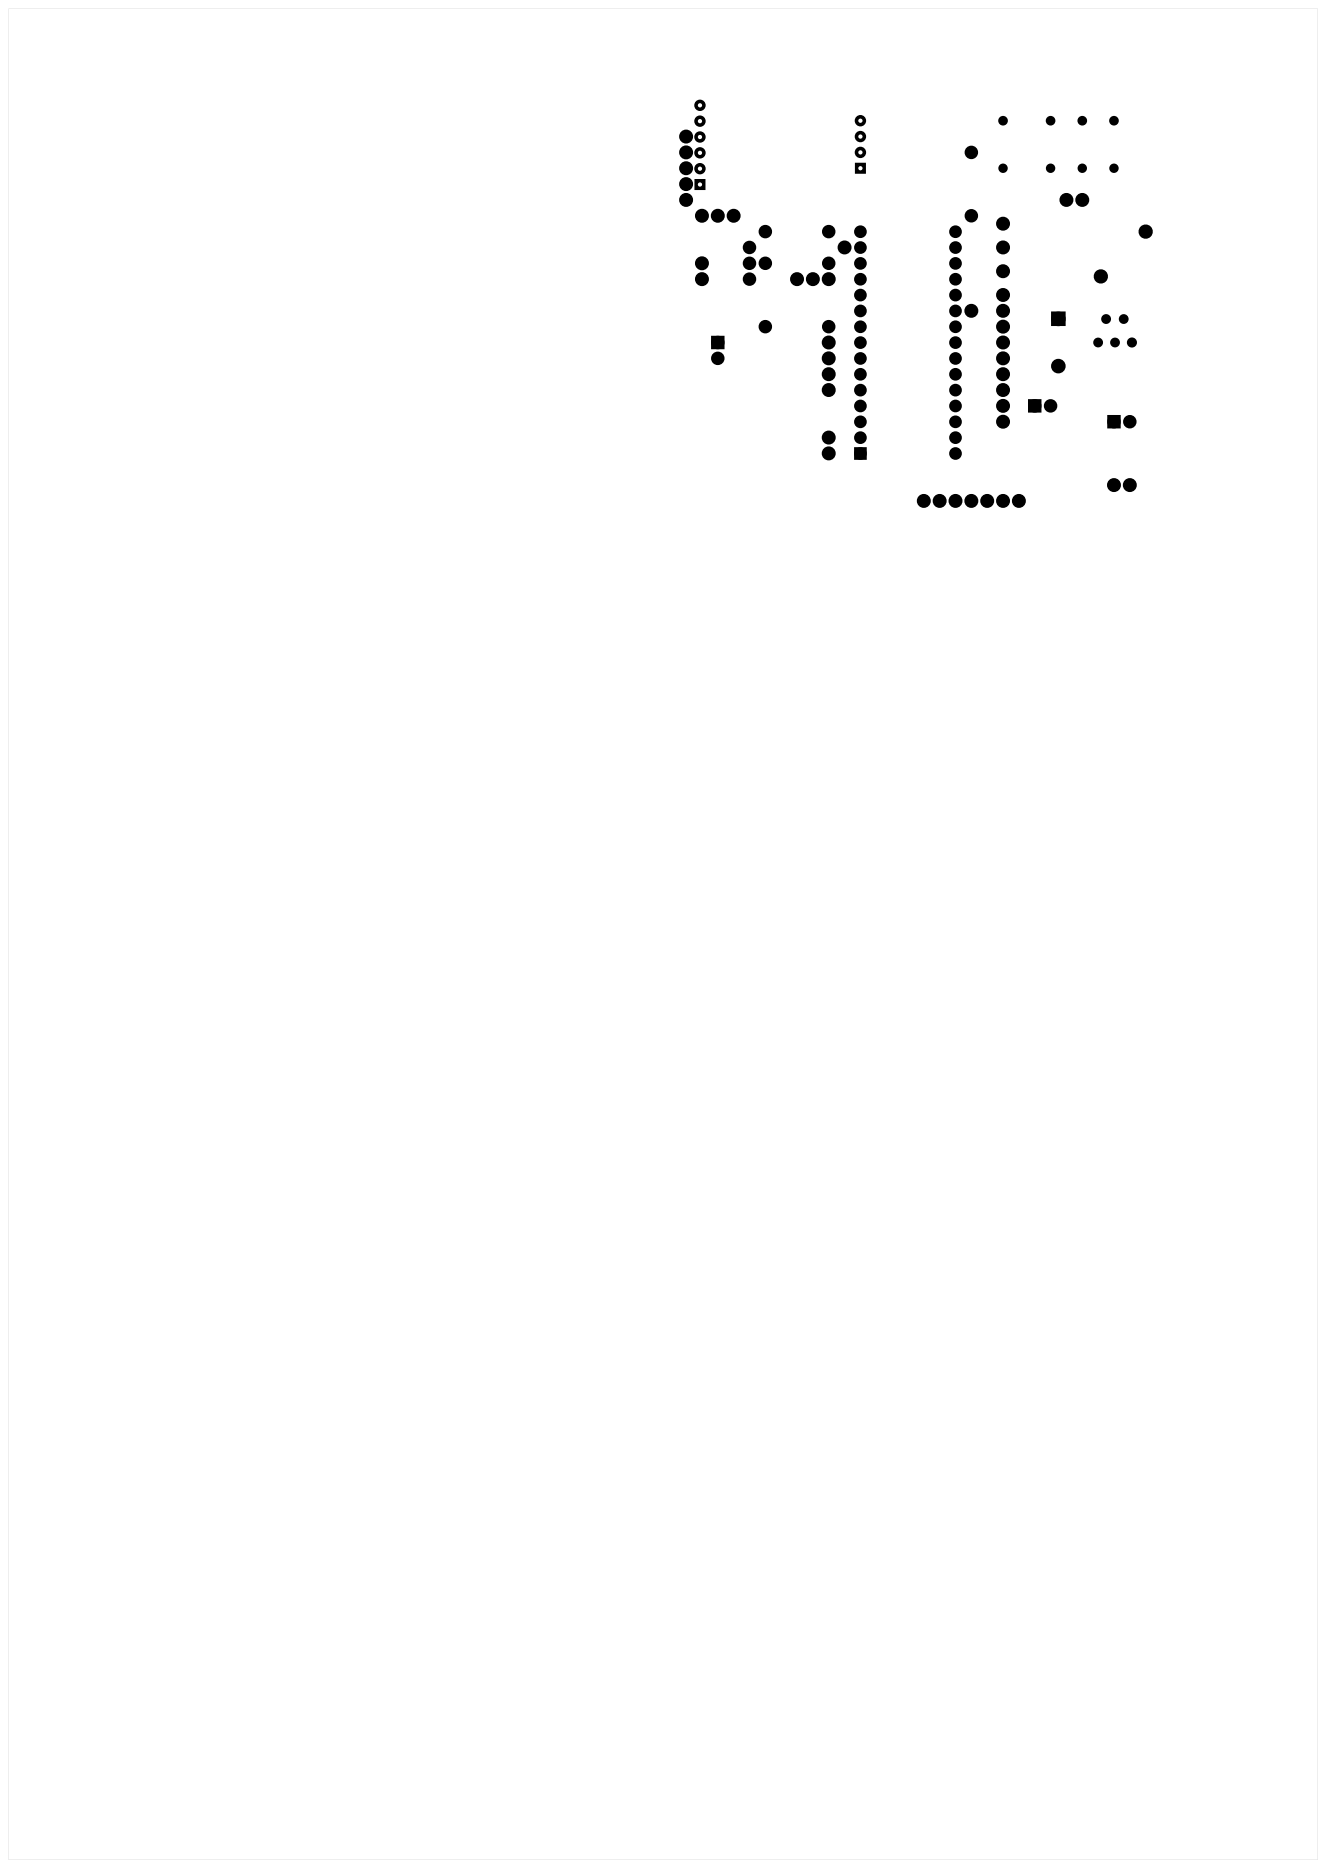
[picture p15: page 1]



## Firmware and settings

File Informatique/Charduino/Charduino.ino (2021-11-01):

#include <EEPROM.h>
#include <Chrono.h>
#include "MoteurEBike.h"
#include <PID_v1.h>
#include <SoftFilters.h>
#include "PinChangeInterrupt.h"
#include "wattmeter.h"
#include "StrengthSensor.h"


/*
 * Paramètres sur lesquels influer:
 *
 *
 *
 *
 *
 */


/////////////////////////////////////////////////
/////////////// Debug ///////////////////////////
/////////////////////////////////////////////////

bool debugPython = 0;     // pour envoyer les données au format attendu par le script python
bool debug = 1;           // pour envoyer les données de debug au format texte dans le moniteur série
bool debugCsv=  0;        // pour envoyer les données de debug au format csv dans le moniteur série
bool debugMotor = 0;      // si aucun moteur n'est branché, pour le simuler
bool debugFrein = 0;      // si aucun interrupteur n'est branché, sur le frein à inertie. Inutilisé actuellement
bool debugCapteur = 0;    // si aucun capteur de force n'est branché, pour le simuler
bool debugOther = 0;      // utilisé à des fins de tests.
bool old = 0;             // pour assurer la compatibilité avec une ancienne version de carte électronique. A garder à 0.
int csvIter = 0;          // compteur d'itération pour l'affichage csv.

/////////////////////////////////////////////////
/////////////// capteur force ///////////////////
/////////////////////////////////////////////////

const int HX711_dout = 7 ; //mcu > HX711 dout pin
const int HX711_sck = 8; //mcu > HX711 sck pin
double capteur_offset = 841.86;

StrengthSensor capteur(HX711_dout, HX711_sck, capteur_offset);


// pour calculer la dérivée du capteur de force. Inutilisé
DifferentialFilter<double, unsigned long> diffCapteur;
Reading<double, unsigned long> rCapteur;
Reading<Differential<double>, unsigned long> dCapteur;


double valeurCapteur;
bool newDataReady = 0;
bool capteurInitialise = 0;
Chrono resetOffsetChrono; // Chrono pour ?
int resetOffsetIter;			// compteur pour compter le nombre d'aller retour sur l'interrupteur brake
MovingAverageFilter<double, double> movingOffset(16); // moyenne lissée sur 16 valeurs
double newOffset, rawValue;


/////////////////////////////////////////////////
/////////////////// EEPROM  /////////////////////
/////////////////////////////////////////////////

// on utilise la mémoire eeprom pour stocker la valeur à considérer comme 0 pour le capteur de force.

int eeprom = 0;

/////////////////////////////////////////////////
/////////////// Frein à inertie /////////////////
/////////////////////////////////////////////////

/*
 * Inutilisée
 *
 * Pour ajouter de la sécurité, l'idée est de mettre un contacteur au niveau du frein à inertie.
 * Quand ça s'ouvre, la remorque commence à aller plus vite que le vélo.
 * L'information est plus basique que celle du capteur de force mais permet d'ajouter une redondance d'informations.
 * Il n'a pas été trouvé encore de position correcte ou de contacteur fiable et robuste.
 * Idée en repos, mais importante à mettre en oeuvre par la suite.
 */

const int frein = debugFrein ? 4 : 5;
Chrono chronoFrein;
bool freinFlag = 0;
int t1 = 300;
int t2 = 1000;
int t3 = 1500;




/////////////////////////////////////////////////
/////////////// Moteur //////////////////////////
/////////////////////////////////////////////////

/*
 * Objet permettant de piloter le moteur au travers du signal de gachette et de frein
 */

MoteurEBike moteur = MoteurEBike();

/////////////////////////////////////////////////
///////////////// PID ///////////////////////////
/////////////////////////////////////////////////

/*
 * Pour lier l'information du capteur de force au signal PWM envoyé dans la gachette, on utilise un PID.
 * https://playground.arduino.cc/Code/PIDLibrary/
 */

// Paramètres à changer:

	double K1[3] = {1, 4, 0.1}; // boost, mode 0 pour les led
	double K2[3] = {1, 2, 0.1}; //marche, mode 1 pour les led
	float betaTab[2]={-6,-3};
	float gammaTab[2]={-10,-6};
	double consigneCapteurTab[2]={-2.0,0.0};

	double sortieMoteur;    //output
	double consigneCapteur = consigneCapteurTab[1]; //setpoint, valeur visée par le PID comme valeur de capteur.
	float pwmMin = 110, pwmMax = 255; // les valeurs minimales et maximales pour le PWM de la gachette.
		                          //110 a été trouvée expérimentalement avec une batterie 48V et un contrôleur Ozo. En deça la roue ne tourne pas.
		                          // ces valeurs sont à tester et corriger en cas de changement de batterie ou contrôleur.

	PID myPID(&valeurCapteur, &sortieMoteur, &consigneCapteur, K1[0], K1[1], K1[2], P_ON_E, REVERSE);
    // Entrée: ValeurCapteur
    // Valeur asservie: SortieMoteur, qui est un PWM allant de pwmMin à pwmMax
    // ConsigneCapteur: Valeur visée pour ValeurCapteur
    // Kp,Ki,Kd, les paramètres dont dépendent l'asservissement du pwm
    // P_ON_E, Proportionnal on Error
    // REVERSE, augmenter la valeur asservie, diminuera l'entrée.

/////////////////////////////////////////////////
//////////////// Etats //////////////////////////
/////////////////////////////////////////////////

enum etats_enum {INITIALISATION,  //0
                 ATTENTE,         //1
                 ROULE,           //2
                 STATU_QUO,       //3
                 DECCELERATION,   //4
                 FREINAGE,        //5
                 MARCHE,          //6
                 RESET_CAPTEUR    //7
                };

int etat = INITIALISATION;

// Ancre paramètre 2

float alpha = 1;  //seuil au dessus duquel le PID se calcule et se lance
float beta = betaTab[0] ; //seuil en deça duquel on passe sur déccélération (pwm=0, pid manual)
float gamma = gammaTab[0]; // seuil en deça duquel on passe sur du freinage


/////////////////////////////////////////////////
//////////// Vitesse moyenne ////////////////////
/////////////////////////////////////////////////

/*
 * Stockage de la vitesse du moteur.
 * Vitesse lue grâce aux capteurs à effet hall du moteur
 * En cas de défaillance de cette information, le système n'est plus utilisable
 */

MovingAverageFilter<double, double> vitesseFiltree(4);
double vitesseMoyenne;
double vitesseInstantanee;



/////////////////////////////////////////////////
///////////// Pin interrupteur debug ////////////
/////////////////////////////////////////////////

int plus = 2;
int moins = 3;
int halt = 4;
bool haltFlag = 0;


/////////////////////////////////////////////////
///////////// Pin controleur ////////////////////
/////////////////////////////////////////////////

int ctrlAlive = 12;     // sur cette pin arrive le 5V de la gachette. Cette information nous renseigne sur l'état du contrôleur.
int ctrlSwitch = 13;    // pin utilisée pour allumer le relais qui activait le contrôleur. Inutilisée depuis que le relais est activé en direct par un interrupteur. A nettoyer
bool isCtrlAlive = debugMotor ? 1 : 0;

/////////////////////////////////////////////////
///////////////// LED  //////////////////////////
/////////////////////////////////////////////////
/*
float maxTraction = 20.0;
float seuilTractionNulle = 0.3;

RemorqueLed led = RemorqueLed(maxTraction, seuilTractionNulle, pwmMin, pwmMax);
*/

int ledPin = 9;

/////////////////////////////////////////////////
///////////////// Wattmetre /////////////////////
/////////////////////////////////////////////////

Wattmeter wattmetre;

int amPin = old ? A4 : A6; // select the input pin for the potentiometer  vert
int vPin = old ? A5 : A7; // select the input pin for the potentiometer   jaune
float amCalib = 28.84;
float vCalib = 18.60;

bool isFlowing;
Chrono flowingChrono; // chrono pour s'avoir depuis quand on envoie un pwm
Chrono stoppedChrono; // chrono pour s'avoir depuis quand on a détecté un arrêt.
int flowingState;



int powerPin = old ? 0 : A3; // pin pour allumer le controleur            Jaune
int motorBrakePin = old ? 0 : A4; // pin pour activer le mode freinage    Vert
int walkPin = old ? 0 : A5; // pin pour activer le mode piéton;           Rouge
Chrono powerChrono, motorBrakeChrono, walkChrono;
bool powerNewState, motorBrakeNewState, walkNewState = 0;
int debounceTime = 100;



bool powerCtrl = old ? 1 : 0;
bool walkMode = 1;
bool motorBrakeMode = 0;


void setup()
{

  Serial.begin(9600);

  Serial.println("###################");
  Serial.println("## version 0.9.7: ");
  Serial.println("## date: 30/10/2021: ");
  Serial.println("## Boulanger ");
  Serial.println("###################");

/*
  On a un nouveau boîtier de contrôle.
  Le mode est lu en fonction de analogRead sur walkPin.
    Avec un pont diviseur de tension, on a empiriquement:
      Mode 1: analogRead = 426 425
      Mode 2: analogRead = 71 72
      Mode 0: analogRead = 1023 (éteint)

*/

  // interrupteur sur la carte
  pinMode(plus, INPUT_PULLUP);
  pinMode(moins, INPUT_PULLUP);
  pinMode(halt, INPUT_PULLUP);
  attachPCINT(digitalPinToPCINT(plus), pluss, CHANGE);
  attachPCINT(digitalPinToPCINT(moins), moinss, CHANGE);
  attachPCINT(digitalPinToPCINT(halt), haltt, CHANGE);

  // freinage inertiel
  pinMode(frein, INPUT_PULLUP);
  chronoFrein.stop();
  attachPCINT(digitalPinToPCINT(frein), freinage, CHANGE);


  // lecture vitesse
  attachPCINT(digitalPinToPCINT(moteur.getUPin()), interruptU, CHANGE);
  attachPCINT(digitalPinToPCINT(moteur.getVPin()), interruptV, CHANGE);

  //PID
  myPID.SetMode(MANUAL);
  myPID.SetOutputLimits(pwmMin, pwmMax);
  myPID.SetSampleTime(200);

  // Controleur
  pinMode(ctrlAlive, INPUT);
  pinMode(ctrlSwitch, OUTPUT);
  digitalWrite(ctrlSwitch, false);
  attachPCINT(digitalPinToPCINT(ctrlAlive), interruptCtrlAlive, CHANGE);

  // Wattmetre
  wattmetre = Wattmeter(amPin, vPin, amCalib, vCalib, 48);

  // boîtier de contrôle
  pinMode(ledPin,OUTPUT);
/*
  flowingChrono.restart();
  flowingChrono.stop();
  stoppedChrono.restart();
  stoppedChrono.stop();

*/
  //capteur
  EEPROM.get(eeprom, capteur_offset);
  Serial.print("## offset: "); Serial.println(capteur_offset);
  capteur.setOffset(capteur_offset);
  capteur.setSamplesInUse(2); //16 le défaut

  pinMode(powerPin, INPUT_PULLUP);
  pinMode(motorBrakePin, INPUT_PULLUP);
  pinMode(walkPin, INPUT_PULLUP);
  attachPCINT(digitalPinToPCINT(powerPin), powerPinInterrupt, CHANGE);
  attachPCINT(digitalPinToPCINT(motorBrakePin), motorBrakePinInterrupt, CHANGE);
//  attachPCINT(digitalPinToPCINT(walkPin), walkPinInterrupt, CHANGE); // n'a plus raison d'être avec nouveau boîtier
  powerChrono.restart();
  powerChrono.stop();
  motorBrakeChrono.restart();
  motorBrakeChrono.stop();
  rCapteur.timestamp = 0;
}

void loop()
{
  // checkCtrl();
  miseAJourVitesse();
  if (capteurInitialise) {
    capteur.update(&newDataReady, &valeurCapteur);
    rCapteur.value = valeurCapteur * 1000;
    rCapteur.timestamp += millis() / 1000;
    diffCapteur.push(&rCapteur, &dCapteur);
  }

  if (valeurCapteur > 30) {
    Serial.println("ERREUR ELM?");
    // valeurCapteur=0;
  }

  wattmetre.update();

  if (powerChrono.elapsed() > debounceTime && digitalRead(powerPin) == powerNewState) {
    powerCtrl = powerNewState;
    powerChrono.restart();
    powerChrono.stop();
    switchCtrl(powerCtrl);
  }

  if (motorBrakeChrono.elapsed() > debounceTime && digitalRead(motorBrakePin) == motorBrakeNewState) {
    motorBrakeMode = !motorBrakeNewState;
    motorBrakeChrono.restart();
    motorBrakeChrono.stop();

    // reset capteur de force
		// Quand on active le frein moteur, si en mode 0
    if (powerCtrl == 0 && etat == INITIALISATION) {
      resetOffsetChrono.restart();
      resetOffsetIter++;
    }

  }


	if(analogRead(walkPin)>300 && analogRead(walkPin)<500 && walkMode==1)
	  setMode(0);
	if(analogRead(walkPin)>50 && analogRead(walkPin)<100 && walkMode==0)
	    setMode(1);


  ////////////////////////////////////////////////////:
  ///////////////////  0  ////////////////////////////
  ////////////////////////////////////////////////////:

  if (etat == INITIALISATION) {

    moteur.setMoteurState(STOPPED);
    sortieMoteur = 0;
    capteur.setThresholdSensor(0.5);
    switchCtrl(powerCtrl);


		// Si ça fait plus de 1000ms que le chrono est lancé, on ne veut pas réinitialiser le capteur, remise à 0.
    if (resetOffsetChrono.elapsed() > 1000) {
      resetOffsetIter = 0;
      resetOffsetChrono.stop();
    }

    if (transition5()) {
      etat = FREINAGE;
    }
    else if (transition01()) {
      etat = ATTENTE;
    }
    else if (transition07()) {
      etat = RESET_CAPTEUR;
    }
  }
  ////////////////////////////////////////////////////:
  ///////////////////  1  ////////////////////////////
  ////////////////////////////////////////////////////:

  else if ( etat == ATTENTE) {

    myPID.SetMode(MANUAL);
    moteur.setMoteurState(STOPPED);
    sortieMoteur = 0;
    capteur.setThresholdSensor(0.5);


		// En mode 1, on arrête le chrono et remet à 0 les itérations pour interdire le reset capteur.
    resetOffsetIter = 0;
    resetOffsetChrono.stop();

		/* a supprimer si on retire le calcul de puissance consommée.
    if (flowingChrono.isRunning()) {
      flowingChrono.restart();
      flowingChrono.stop();
    }
		*/

    if (transition5()) {
      etat = FREINAGE;
    }
    else if (transition0())
      etat = INITIALISATION;
    else if (transition12())
      etat = ROULE;
    else if (transition15())
      etat = FREINAGE;
  }

  ////////////////////////////////////////////////////:
  ///////////////////  2  ////////////////////////////
  ////////////////////////////////////////////////////:

  else if (etat == ROULE) {
    moteur.setMoteurState(SPINNING);
    myPID.SetMode(AUTOMATIC);
    miseAJourPID();
    if (!flowingChrono.isRunning()) {
      flowingChrono.restart(); //
    }

    capteur.setThresholdSensor(0.0);
    //   flowingOrNot();


    if (transition5()) {
      etat = FREINAGE;
    }
    else if (transition0())
      etat = INITIALISATION;
    else if (transition23())
      etat = STATU_QUO;
  }

  ////////////////////////////////////////////////////:
  ///////////////////  3  ////////////////////////////
  ////////////////////////////////////////////////////:

  else if ( etat == STATU_QUO) {
    moteur.setMoteurState(SPINNING);

    myPID.SetMode(AUTOMATIC);
    miseAJourPID();


    if (transition5()) {
      etat = FREINAGE;
    }
    else if (transition0())
      etat = INITIALISATION;
    else  if (transition32())
      etat = ROULE;
    else if (transition34())
      etat = DECCELERATION;
  }

  ////////////////////////////////////////////////////:
  ///////////////////  4  ////////////////////////////
  ////////////////////////////////////////////////////:

  else if ( etat == DECCELERATION) {

    moteur.setMoteurState(STOPPED);
    myPID.SetMode(MANUAL);
    sortieMoteur = 0;

    if (transition5()) {
      etat = FREINAGE;
    }
    else if (transition0())
      etat = INITIALISATION;
    else  if (transition42())
      etat = ROULE;
		// c'était en état == ATTENTE, càd  état 1. Pourquoi?
    //  etat = ATTENTE;
    else if (transition45())
      etat = FREINAGE;
  }


  ////////////////////////////////////////////////////:
  ///////////////////  5  ////////////////////////////
  ////////////////////////////////////////////////////:

  else if (etat == FREINAGE) {

    myPID.SetMode(MANUAL);
    moteur.setMoteurState(BRAKING);
    sortieMoteur = 0;
    capteur.setThresholdSensor(0.5);

		// En mode 5, on arrête le chrono et remet à 0 les itérations pour interdire le reset capteur.
    resetOffsetIter = 0;
    resetOffsetChrono.stop();

		/*
    if (flowingChrono.isRunning()) {
      flowingChrono.restart();
      flowingChrono.stop();
    }
		*/

    if (transition5()) {
      etat = FREINAGE;
    }
    else if (transition0())
      etat = INITIALISATION;
    else   if (transition52())
      etat = ATTENTE; //ROULE;
    else if (transition51())
      etat = ATTENTE;
  }

  ////////////////////////////////////////////////////:
  ///////////////////  7  ////////////////////////////
  ////////////////////////////////////////////////////:

  else if (etat == RESET_CAPTEUR) {
    /*
       On attend 500ms puis la valeur actuelle du capteur est stockée et lissée sur 32 valeurs
    */


		/*
			Je comprends pas le rapport au nombre 10.
		*/
    if (resetOffsetIter != 10)
      resetOffsetChrono.restart();
    resetOffsetIter = 10;
    if (resetOffsetChrono.elapsed() > 500) {
      rawValue = capteur.getRaw();
      movingOffset.push(&rawValue, &newOffset);
    }
    if (transition70()) {
      //  Serial.print(" ## capteur valeur: ");Serial.println(newOffset);
      EEPROM.put(eeprom, newOffset);
      capteur.setOffset(newOffset);
      resetOffsetIter = 0;
      resetOffsetChrono.restart();
      resetOffsetChrono.stop();
      etat = INITIALISATION;
    }
  }


  else {
     Serial.println("Sortie de cas");
  }


  if (debugPython) {

    envoi(vitesseMoyenne);
    envoi(sortieMoteur);
    envoi(valeurCapteur);
    envoiInt(myPID.GetKi());
    envoiFin();
  }
  else if (debugCsv) {
    printCsv();
  }
  else if (debug) {
    debugMessage();
  }
  else {

  }
  moteur.mettreLesGaz(sortieMoteur);


  // gestion de la led
  if(sortieMoteur>0 && vitesseMoyenne<1.0){
    if(millis()%3000>500)
      digitalWrite(ledPin,HIGH);
    else
      digitalWrite(ledPin,LOW);
  }
  else if(etat == RESET_CAPTEUR){
    if(millis()%1000>500)
      digitalWrite(ledPin,HIGH);
    else
      digitalWrite(ledPin,LOW);
  }
  else{
    digitalWrite(ledPin,HIGH);
  }
}


bool transition01() {
  //Serial.print("transition 01"); Serial.print(" - "); Serial.print(etat == INITIALISATION); Serial.print(" - "); Serial.print(initialisationCapteur()); Serial.print(" - "); Serial.print(vitesseMoyenne < 1.0); Serial.print(" - "); Serial.print(isCtrlAlive);
  //Serial.println();
  return (etat == INITIALISATION && initialisationCapteur() && vitesseMoyenne < 1.0 && isCtrlAlive);
}
bool transition07() {
  return (etat == INITIALISATION && resetOffsetIter > 3 && !isCtrlAlive);
}
bool transition12() {
  return (etat == ATTENTE && valeurCapteur > alpha && vitesseMoyenne > 1.0 && isCtrlAlive);
}
bool transition15() {
  return (etat == ATTENTE && valeurCapteur < gamma || chronoFrein.elapsed() > t1 && isCtrlAlive);
}
bool transition23() {
  return (etat == ROULE && (valeurCapteur < 0.5 || chronoFrein.elapsed() > t1) && vitesseMoyenne > 0 && isCtrlAlive);
}
bool transition32() {
  return (etat == STATU_QUO && valeurCapteur > alpha && !chronoFrein.isRunning() && isCtrlAlive);
}
bool transition34() {
  return (etat == STATU_QUO && (valeurCapteur < beta && valeurCapteur > gamma ) || chronoFrein.elapsed() > t2 && isCtrlAlive);
}
bool transition42() {
  return (etat == DECCELERATION && valeurCapteur > alpha && !chronoFrein.isRunning() && isCtrlAlive);
}
bool transition45() {
  return (etat == DECCELERATION && valeurCapteur < gamma || chronoFrein.elapsed() > t3 && isCtrlAlive);
}
bool transition52() {
  return (etat == FREINAGE && (valeurCapteur > 2 * alpha || (valeurCapteur > alpha && vitesseMoyenne < 1.0 )) && !chronoFrein.isRunning() && isCtrlAlive && !motorBrakeMode);
}
bool transition51() {
  return (etat == FREINAGE && !chronoFrein.isRunning() && vitesseMoyenne < 1.0  && valeurCapteur >= 0.0 && valeurCapteur < alpha && isCtrlAlive  && !motorBrakeMode);
}
bool transition70() {
  return (etat == RESET_CAPTEUR && !isCtrlAlive && !motorBrakeMode && resetOffsetChrono.elapsed() > 3000);
}
bool transition0() {
  return (!isCtrlAlive || !initialisationCapteur());
}

bool transition5() {
  return (isCtrlAlive && (motorBrakeMode || valeurCapteur < gamma));
}


/*
   interruptions
*/

void interruptU()
{
  moteur.interruptU();
}

void interruptV()
{
  moteur.interruptV();
}
void interruptCtrlAlive()
{
  if (digitalRead(ctrlAlive))
    isCtrlAlive = 1;
  else
    isCtrlAlive = 0;
}


void freinage() {
  if (debugFrein) {
    if (!digitalRead(frein) && !chronoFrein.isRunning()) {
      chronoFrein.start();
    }
    else if (digitalRead(frein) && chronoFrein.isRunning()) {
      chronoFrein.restart();
      chronoFrein.stop();
    }

    if (!digitalRead(frein)) {
      vitesseMoyenne = vitesseMoyenne ? 0.0 : 10.0;
    }
  }
  else {
    if (digitalRead(frein) && !chronoFrein.isRunning()) {
      chronoFrein.start();
    }
    else if (!digitalRead(frein) && chronoFrein.isRunning()) {
      chronoFrein.restart();
      chronoFrein.stop();
    }
  }
}
void pluss() {
  //if((debugCapteur || debugOther) && !digitalRead(plus))
  //  Kd+=0.1;
}
void moinss() {
  // if((debugCapteur || debugOther) && !digitalRead(moins))
  //   Kd-=0.1;
}
void haltt() {
  // if(!digitalRead(halt)){
  //   vitesseMoyenne=vitesseMoyenne?0.0:10.0;
  // }
}


void powerPinInterrupt() {
  if (digitalRead(powerPin)) {
    powerNewState = true;
    powerChrono.restart();
    //powerCtrl=1;
  }
  else {
    powerNewState = false;
    powerChrono.restart();
  }


  // switchCtrl(powerCtrl);
}
void motorBrakePinInterrupt() {
  /*
      Interruption pour activer le frein moteur

      cette interruption sera utilisée aussi pour réinitialiser le zéro du capteur de force quand le controleur est éteint.
      L'activer 3 fois de suite fera passer dans l'état 6 qui est celui de recalcul du zéro du capteur de force.
  */

  if (digitalRead(motorBrakePin)) {
    //motorBrakeMode=1;
    motorBrakeNewState = true;
    motorBrakeChrono.restart();

  }
  else {
    motorBrakeNewState = false;
    motorBrakeChrono.restart();
  }
}


//void walkPinInterrupt() {
void setMode(int mode){
  if (mode==1){
    walkMode = 1;
    consigneCapteur = consigneCapteurTab[1];
    beta = betaTab[1];
    gamma = gammaTab[1];
    myPID.SetOutputLimits(pwmMin, pwmMax);

  }
  else{
    walkMode = 0;
    beta = betaTab[0];
    gamma = gammaTab[0];
    consigneCapteur = consigneCapteurTab[0];
    myPID.SetOutputLimits(pwmMin, pwmMax);

  }

  setPIDMode(walkMode);
}


/*
   Fonctions annexes
*/

void setPIDMode(bool walkOrNot) {
  if (walkOrNot) {
    myPID.SetTunings(K2[0], K2[1], K2[2]);
  }
  else {
    myPID.SetTunings(K1[0], K1[1], K1[2]);
  }
}
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

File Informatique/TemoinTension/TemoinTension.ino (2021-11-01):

/*


    Courbe d'interpolation linéaire: 16.225*U-1.17 = Analog
    42V limite basse --> 680 Analog
    54.6 limite haute --> 884

    Si analog>870: Plein, diode fixe
    Echelon entre 870 et 690 plus c'est bas, plus la période de clignotement augmente

*/

#include <Arduino.h>
#include <SoftFilters.h>

int sensorPin = A0;    // select the input pin for the potentiometer
int ledPin = 6;      // select the pin for the LED
int sensorValue = 0;  // variable to store the value coming from the sensor

const int highValue=870.;
const int lowValue=690;
float diffValue=float(highValue-lowValue);

MovingAverageFilter<int, int> movAvg(5);
int avg;

int niveau=0;

void setup() {
  // declare the ledPin as an OUTPUT:
  pinMode(ledPin, OUTPUT);
  Serial.begin(9600);
}

/*
 * Renverra 10 sir c'est presque 100%
 * Renverra 1 si c'est 10%
 */
int calculerNiveau(int tensionAnalogique)
{
  
  return abs(10-round(((highValue-tensionAnalogique)/diffValue*10)));
}


void loop() {
  // read the value from the sensor:
  sensorValue = analogRead(sensorPin);
  movAvg.push(&sensorValue, &avg);
  niveau=calculerNiveau(avg);
  Serial.print("niveau: ");Serial.print(niveau);

  if(avg>=highValue)
    digitalWrite(ledPin,HIGH);
  else if(avg<highValue && avg>=lowValue){
    Serial.println(" entre les deux");
    for(int i=0; i<niveau;i++){
      digitalWrite(ledPin,HIGH);
      delay(200);
      digitalWrite(ledPin,LOW);
      delay(200);
    }
    delay(1000);
  }
  else if(avg<lowValue){
    Serial.println(" tension basse");
    digitalWrite(ledPin,HIGH);
    delay(200);
    digitalWrite(ledPin,LOW);
    delay(200);
    digitalWrite(ledPin,HIGH);
    delay(200);
    digitalWrite(ledPin,LOW);
    delay(200);
    digitalWrite(ledPin,HIGH);
    delay(200);
    digitalWrite(ledPin,LOW);
    delay(500);
    digitalWrite(ledPin,HIGH);
    delay(500);
    digitalWrite(ledPin,LOW);
    delay(500);
    digitalWrite(ledPin,HIGH);
    delay(500);
    digitalWrite(ledPin,LOW);
    delay(500);
    digitalWrite(ledPin,HIGH);
    delay(500);
    digitalWrite(ledPin,LOW);
    delay(500);
    digitalWrite(ledPin,HIGH);
    delay(200);
    digitalWrite(ledPin,LOW);
    delay(200);
    digitalWrite(ledPin,HIGH);
    delay(200);
    digitalWrite(ledPin,LOW);
    delay(200);
    digitalWrite(ledPin,HIGH);
    delay(200);
    digitalWrite(ledPin,LOW);
    delay(1000);
  }
  else{
    Serial.println(" ???");
    digitalWrite(ledPin,HIGH);
    delay(100);
    digitalWrite(ledPin,LOW);
    delay(100);
    digitalWrite(ledPin,HIGH);
    delay(500);
    digitalWrite(ledPin,LOW);
    delay(500);
  }
}

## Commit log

2020-10-07 initialisation lecture de la vitesse et envoi à python PID configuré, il reste à déterminer les constantes
2020-10-08 gestion des données plus fine dans graphVitesse2.py, possibilité de tout afficher Reste à trouver des paramètres acceptables
2020-10-09 affinement des paramètre PID gestion de l envoi d info à Python pour un graphique détaillé gestion augmentation consigne par interrupteur
    Test sur terrain fait avec batterie 36V et contrôleur 25A, ça fonctionne. Sur du plat 17km/h, en montée, ça pousse, peut-être pas assez rapidement mais c est encourageant.
    A voir pour rendre plus réactif
2020-10-24 ajout lecture capteur et affichage sur led désactivation du PID Moteur par haltFlag
    [20201020-14h37m30s.csv, 20201020-14h37m56s.csv, 20201020-14h42m15s.csv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]
2020-10-24 PID appliqué à la valeur du capteur de traction
    [20201024-17h05m00s.csv, 20201024-17h09m34s.csv, 20201024-17h11m49s.csv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]
2020-11-09 Ajout d'une rangée de led pour affichage PWM Ajout d'une variable pour définir debug via Python ou moniteur série Définition PWMmin PWMmax Définition d'une valeurCapteurSeuil en deça de laquelle, si 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
    [20201026-15h22m45s première sortie 12-6-0.1.ods, 20201026-15h26m11s deuxime sortie 6.5 3.25 0.1 .ods]
2020-11-16 création du fichier fritz
    [20201020-14h37m30s.csv, 20201020-14h37m56s.csv, 20201020-14h42m15s.csv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]
2020-11-17 ajout chronoFrein Ajout allumage CTRL via mosfet Ajout frein moteur (Fritz) Ajout diode controle allumage CTRL via gachette (fritz)
    [PID_Basic.fzz]
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2020-11-17 nettoyage code creation logie etat machine reste à faire des tests
    [PID_Basic.fzz]
2020-11-23 ajout fonctions de transitions d'état Ajout debugMotor Ajout allumage du controleur par relais/mosfet
    [PID_Basic.fzz]
2020-11-26 nouvelle carte électronique avec activation du controleur par l'arduino convertisseur 60V->5V nettoyage du code
    [PID_Basic.fzz, alimentation.fzz]
2020-11-27 le frein à inertie a été désactivé avec un serre-joint car le mouvement avec le ressort créait trop d'interférence dans le capteur de force les valeurs du capteur de force s'échelonne entre -16 et 6,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
    Les paramètres du PID ont été changés aussi
    TODO
    Revoir un peu les transitions entre état
    Corriger les paramètres du PID, y avait oscillation
    Penser à mettre deux modes pour le PID, un pour le démarrage, un pour pendant la course (pas besoin d'être nerveux outre mesure)
    Comment tarer correctement le caapteur de force?
    Si le cable PWM est débranché on tombe en état 0. Rebranché, on y reste, corriger la transition 01
    [graphVitesse.py]
2020-12-27 ajout du wattmetre
    [calcul shunt.ods]
2020-12-28 nettoyage du code incorporation du code des led, du capteur de force, du moteur dans des bibliothèques séparées fonctionnement identique
    A Faire:
    - mettre à jour le schéma électrique
    - corriger le calcul du courant électrique qui affiche un faux positif (ou corriger calcul de la puissance...)
    [PID_Basic.fzz]
2020-12-31 Côte de chez Vinvin: réussie! Le 31 décembre 2020 est à marquer dans l'Histoire du Vélo et de Véloma, la charrette a monté la côte de chez Vinvin chargée à 150kg malgré le gravier du début de course.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
2021-01-03 ok pour test avec boulanger, modulo le capteur de frein qui est déconnecté
    [PID_Basic.fzz]
2021-01-07 ajout interrupteur powerCtrl, mode piéton, mode freinage, ajout d'une transition pour tout pointer vers 5 quand mode freinage
    [20210107-18h21m22s.csv, 20210107-18h22m46s.csv, 20210107-18h24m38s.csv]
2021-01-08 Redéfinition des paramètre PID par défaut en mode piéton Retrait passage état 2 vers état 3 Ajout transition5 avec compression du capteur Ajout gestion mode marche Ajout fonction setPIDMode pour pass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
    [20210107-18h21m22s.csv, 20210107-18h22m46s.csv, 20210107-18h24m38s.csv]
2021-01-08 ajout changement seuil pourn le capteur. Est-ce que ça marche?
2021-01-20 avec nouveau paramètres PID. PBLM: perturbations elm des câbles PBLM: fausses tractions détectées par le capteur de force PBLM: quand la barre est tordue, ça envoie de mauvaises info au capteur TODO: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
2021-02-01 correction de flowingOrNot
2021-02-02 il faut débrancher les capteurs effet hall pour pouvoir faire avancer la roue correctement. Sinon on manque un signal et le moteur plante. Ca marche mieux depuis. TODO: pour récupérer quand même la v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
    [20210201 logs.ods]
2021-02-17 Côte de Vinvin avec 200kg ok
    Avoir les capteurs effet hall pour la lecture de la vitesse et le mode sinusoidale est primordial, la roue de Léandro a été réparée.
    Le seuil d'activation du frein moteur a été baissé à -15.
    Pour avoir une vraie assistance, il est nécessaire de 'tricher' en initialisant le capteur en contrainte de compression. Les départs et le roulage s'en trouvent améliorés tout en gardant le freinage
    TODO: voir à définir un autre seuil pour le PID, -1 plutôt que 0 par exemple.
    Les paramètres du PID ont été revus à la baisse aussi. 1,3,0 voire 1,2,0 suffisent sans avoir trop d'acoups au démarrage.
    On ressent et entend des acoups pendant le roulage parce qu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
2021-02-17 Avoir les capteurs effet hall pour la lecture de la vitesse et le mode sinusoidale est primordial, la roue de Léandro a été réparée. Le seuil d'activation du frein moteur a été baissé à -15. Pour avo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
    [20201026-15h22m45s première sortie 12-6-0.1.ods, 20201026-15h26m11s deuxime sortie 6.5 3.25 0.1 .ods, 20210201 logs.ods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]
2021-02-18 création pcb
    [Charduino.fzz]
2021-05-28 livraison MAAD93
    [Charduino.fzz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]
2021-06-12 Concarneau Gestion de deux modes Abaissement de gamma pour freiner plus tôt
    [Wattmetre.fzz, calibration et autres calculs.ods]
2021-07-06 gestion du bouton de frein, gestion du bouton des modes
2021-07-06 utilisation de l'eeprom pour la lecture de la dernière valeur de tarage du capteur de force
2021-07-06 diminution nombre d'échantillon pour le capteur de force pour augmenter en réactivité et arrangement des paramètres par rapport au sélecteur de mode
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2021-07-20 modification des paramètres PID selon ceux utilisés sur la remorque boumboum. Passage du max du mode lent à 220 au lieu de 180. modif info de debug
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2021-09-16 ajout commentaire pour resetOffset qui est obscur
    [Charduino.ino]
2021-09-17 Gestion plus fine du reset du capteur
    [Charduino.ino]
2021-09-17 v0.9.6 MAAD93
    RemorqueLed
    Ajout fonction ledWait pour l'initialisation
    Charduino.ino
    mise à 0 du PWM pour état 0, 3 et 4.
    Ca semble corriger les erreurs lors des redémarrages
    [Charduino.ino, RemorqueLed.cpp, RemorqueLed.h]
2021-09-30 Modification Mise en forme du répertoire
    [Charduino.fzz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]
2021-10-30 Modification: documentation
    [calculs gachette.ods]
2021-10-30 Modification: Charduino.ino utilisation du boîtier de contrôle avec la PCB mise en ordre des paramètres beta/gamma/K1,K2 petite correction dans la machine-état transition42 pwmMax en mode lent aussi.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
    [Charduino.ino]
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2021-11-01 Modification: clignotement: à 1/2 lors du reset à 5/6 en cas de panne moteur Ajout: arduino pour contrôler le niveau de batterie indépendamment du Charduino
    [Charduino.ino, TemoinTension.ino]
